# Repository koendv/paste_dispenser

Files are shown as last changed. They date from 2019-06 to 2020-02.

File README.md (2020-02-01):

# Solder Paste Dispenser

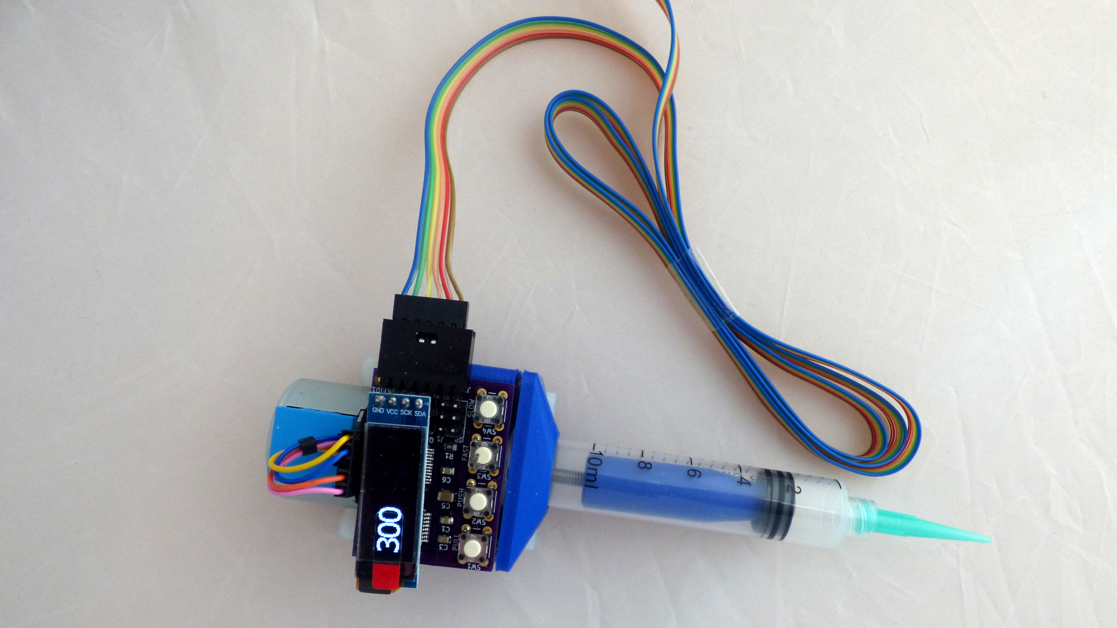
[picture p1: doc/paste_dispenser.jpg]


This is a solder paste dispenser. The controller supports unipolar and bipolar stepper motors, a foot pedal switch, an OLED display, a LED that blinks faster when the motor runs faster, and a menu system. The board has been designed with easy soldering in mind, using components size 0805 and up.

## Foot switch
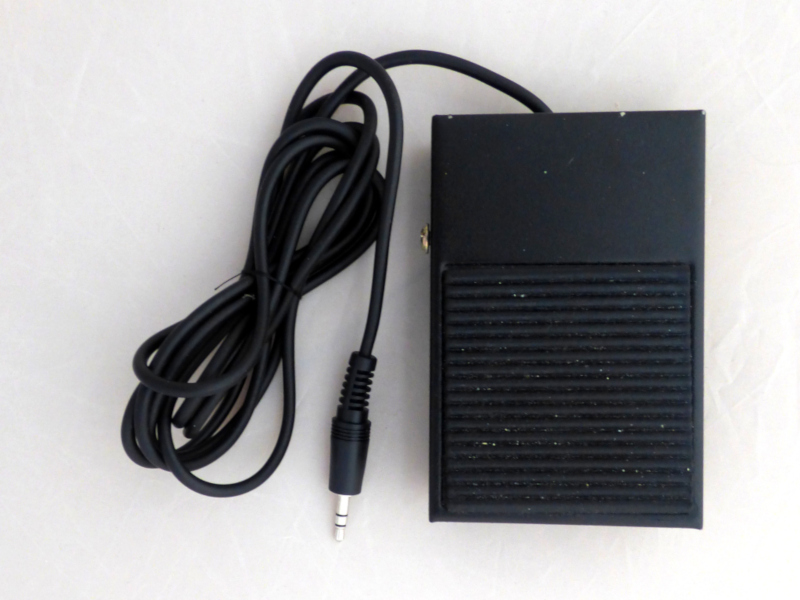
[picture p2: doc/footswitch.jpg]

Dispensing can be initiated either by pressing the *push* button on the dispenser, or by pushing down a foot pedal switch.

A foot pedal switch has the advantage that it frees up a hand. Using a foot switch is also more stable; pushing a button on the solder dispenser always moves the syringe tip a little bit.

Suitable foot pedals are [Adafruit product ID 423](https://www.adafruit.com/product/423) and [Sparkfun COM-11192](https://www.sparkfun.com/products/11192), and their equivalents at ebay and aliexpress.

These foot pedal switches are simple on/off switches, normally open. Speed controller foot pedals with a potentiometer will **not** work.

## Display

The display shows the motor speed.

The OLED display is a generic OLED module 0.91" diagonal, 128x32 pixel, I2C, SSD1306, as found on ebay, aliexpress and [others](https://www.google.com/search?q=OLED+module+0.91%22+128x32+I2C+SSD1306+price). Before buying, check the module has a 4-pin connection - GND, VCC, SDA, SCK - and uses a SSD1306 controller. The display *ought* not to touch any of the components below, but you can always put a bit of Kaptan tape on the back of the display, just to make sure.

The OLED display is optional. If you choose not to install the OLED display you can still check stepper speed on the serial console.

## Menu

There is a settings menu on the serial port. The serial port runs at 115200, 8N1, no flow control. Access the menu using a vt100 ansi terminal emulation, e.g. [PuTTY](https://putty.org/) on Windows, or *minicom* on Linux. On Android, use an USB OTG adapter and *Serial USB Terminal*. The settings menu allows you to configure forward speed, backward speed, pullback, and microstepping, and to store and recall these settings from non-volatile memory. The menu looks like this:

	[f] Forward speed 125 steps/sec
	[s] Forward steps 0 steps
	[b] Backward speed 500 steps/sec
	[d] Pullback delay 2000 millisec
	[p] Pullback steps 0 steps
	[m] Microstepping 2
	[n] Profile number 0
	[r] Restore profile
	[w] Save profile
	[h] Help

### Speed
Forward speed can be set using the *faster*/*slower* buttons on the dispenser itself or using the console menu.

If *forward steps* is zero, the syringe plunger is pushed down as long as you press the *push* button or the foot switch pedal. This is useful for making beads, and the normal setting when dispensing solder paste. If *forward steps* is non-zero, pushing the *forward* button or the foot switch moves the plunger down exactly the number of steps in the settings. This is useful for making precise, repeatable dots, e.g. as a glue or lubricating oil dispenser.

Backward speed can only be set using the console menu.

### Pullback
Sometimes liquid keeps oozing out after you stop dispensing. If *pullback steps* is non-zero, then after a *pullback delay* period of inactivity the plunger will move back *pullback steps*, to stop liquid oozing out. How successful this is and how many steps the plunger needs to pull back to stop the oozing depends upon the viscosity of the liquid. *Pullback* works better with low viscosity liquids than with high viscosity paste. Pullback is interesting if you use this as a dispenser for e.g. cyanoacrylate glue.

### Microstepping
The controller supports up to 1/64 microstepping. This is open loop voltage control microstepping.
Choose speed and microstepping that goes well with your stepper motor. This may take a bit of trial and error. Default is half-stepping, suitable for 28BYJ-48 steppers .

### Saved Profiles

Once you have found a setting that works, you can save it for later. Up to five profiles can be saved. These profiles are remembered even when the power is turned off. After power-up the last saved settings are used.

## Power supply

If you want to play it safe, use a 5.0V 1A phone charger as power supply. The TB6612 stepper motor driver IC supports 5V 1.2A continuous, but can be damaged by higher currents. Using a power supply with a maximum current less than 1.2A protects the driver IC in case of short circuit or stall.

The voltage range is 4.5V to 5.5V. More than 5.5V is too much for the atmega328p microcontroller; less than 4.5V and the TB6612 stepper driver stops working.

The board has a MOSFET for reverse polarity protection.

## Connecting everything

The controller board has four headers:

* J1 is the ISP connector for downloading the initial firmware to the atmega microcontroller.
* J2 connects to an USB to serial adapter (pins +5V, RX, TX, GND) and the footswitch (pins FTSW, GND). The footswitch is optional, but very handy.
* J3 is the connector for the stepper motor. Both unipolar and bipolar steppers can be connected. Connect one coil to pins A1 and A2, and one coil to pins B1 and B2. Connect the center tap of unipolar steppers to pin GND.
* J4 is the connector for the optional OLED display. Solder a 4-position female Dupont housing here.

## Bootstrapping

The first compile is the hardest.

Open the Arduino IDE. Compile the *paste dispenser* sketch, with these settings:

* Board: Arduino Pro or Pro Mini,
* Processor: Atmega328P (5V, 16MHz).

Generate an Intel Hex file with _Sketch -> Export Compiled Binary_. This creates two .hex files in the project directory, `arduino.ino.eightanaloginputs.hex` and `arduino.ino.with_bootloader.eightanaloginputs.hex`. The hex file we need is the one with the bootloader.
The ISP programmer is an arduino with the same logic levels as the target system. As the solder paste dispenser uses 5V logic, we need an Arduino with 5V logic levels as ISP programmer. Connect a 5V Arduino, e.g. an Arduino Uno, to your system. Compile and upload the _File -> Examples -> ArduinoISP_ sketch to the Uno. Connect the Arduino Uno to the solder paste dispenser board as follows:

Signal|Uno    |ISP pin
------|-------|--------
RST	|Uno pin 10|5
MOSI|Uno pin 11|4
MISO|Uno pin 12|1
SCK|Uno pin 13|3
VCC|Uno 5V|2
GND|Uno GND|6

Find `avrdude` in your Arduino IDE directories, change to the appropriate directory and do the following incantation:

	koen@raspberrypi:/opt/arduino-1.8.9/hardware/tools/avr $ ./bin/avrdude -C ./etc/avrdude.conf -p m328p -P /dev/ttyACM0 -c avrisp -b 19200 -U flash:w:/home/koen/src/paste_injector/arduino/arduino.ino.with_bootloader.eightanaloginputs.hex

where `/dev/ttyACM0` is the usb port of your Arduino Uno. Flashing should take about 20 seconds, and ends with "`xxx bytes of flash verified`" and "`Fuses OK`".

Set the fuses of the atmega328p for an external resonator at 16MHz:

	koen@raspberrypi:/opt/arduino-1.8.9/hardware/tools/avr $ ./bin/avrdude -C ./etc/avrdude.conf -c avrisp -p m328p -P /dev/ttyACM0 -b 19200  -U lfuse:w:0xff:m -U hfuse:w:0xda:m -U efuse:w:0xfd:m

The avrdude output ought to say: ```avrdude: safemode: Fuses OK (E:FD, H:DA, L:FF)```

If you just want to read the fuses:

	koen@raspberrypi:/opt/arduino-1.8.9/hardware/tools/avr $  ./bin/avrdude -C ./etc/avrdude.conf -c avrisp -p m328p -P /dev/ttyACM0 -b 19200 -U lfuse:r:-:i -v

This finishes writing bootloader and sketch to the solder paste dispenser. Disconnect the Arduino Uno. The atmega328p now contains a bootloader. Sketches can now be uploaded using the solder paste dispenser serial port.

## Firmware

The solder paste dispenser is an arduino system. Once the bootstrap loader has been installed the solder paste dispenser can be programmed using the arduino IDE.

To avoids spurious resets when connecting to the serial port, there is no capacitor between DTR and reset. But this also means that if you want to develop firmware for this board there is no automatic reset before uploading. Three options:

* Upload firmware using the ISP connector. This has to be done at least once, to upload the bootloader.
* Use the serial port to upload. This is what I usually do. Before uploading connect RST and ground with a Dupont jumper wire. RST and ground are next to each other on the ISP connector. In the Arduino IDE, click Sketch -> Upload, count to three and remove the jumper wire.
* When developing connect a 100n capacitor between serial adapter DTR and ISP connector RST pin. This allows the IDE to reset the microcontroller automatically just before uploading using the serial port.

## Soldering your own
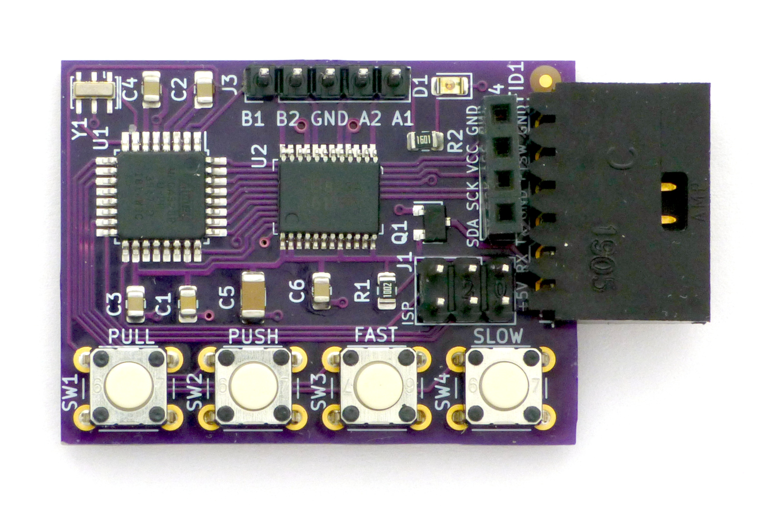
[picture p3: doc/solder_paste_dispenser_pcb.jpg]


The github contains arduino source and kicad pcb design files. You'll find the [schematic](https://github.com/koendv/paste_dispenser/raw/master/kicad/paste_dispenser/paste_dispenser_schematic.pdf), the [board layout](https://github.com/koendv/paste_dispenser/raw/master/kicad/paste_dispenser/paste_dispenser_board.pdf), and the [bill of materials](https://github.com/koendv/paste_dispenser/blob/master/kicad/paste_dispenser/paste_dispenser.csv). This is a link to the pcb as an orderable [shared project at oshpark](http://www.oshpark.com/shared_projects/V5txbi41), and these are the components as a [shared project at Mouser](https://www.mouser.com/ProjectManager/ProjectDetail.aspx?AccessID=61ff8d7d43). Here are [zipped gerbers](https://github.com/koendv/paste_dispenser/raw/master/kicad/paste_dispenser/gerbers.zip) for pcb manufacturing at [jlcpcb](https://jlcpcb.com/).

If you prefer not to solder SMD's you can also build the controller on a breadboard or as a through-hole pcb, as in this [fritzing sketch](https://github.com/koendv/paste_dispenser/raw/master/fritzing/paste_dispenser_fritzing_breadboard.pdf) of a 5V 16MHz Arduino Pro Mini and a TB6612 breakout module.

## Printing your own
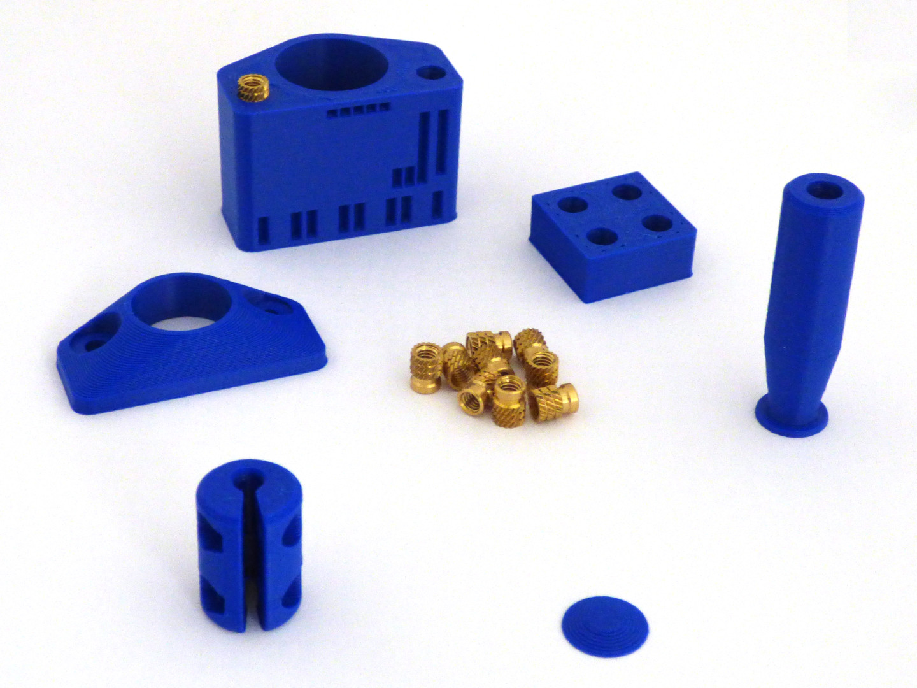
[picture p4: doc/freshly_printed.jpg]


Leave part orientation as is when imported into PrusaSlicer. Designed to print without support.

The [openscad/](https://github.com/koendv/paste_dispenser/tree/master/openscad) directory contains the .stl files for [3d-printing](https://www.treatstock.com/c/seaside-3d) the mechanical part of the solder paste dispenser in ABS using FDM. These parts need finishing as follows:

* Take the workpiece [insert_practice](https://github.com/koendv/paste_dispenser/blob/master/openscad/aerzetix-C19143/insert_practice.stl) and place 4 heat-set inserts, as a test. Set your soldering iron to the filament extrusion temperature used during 3D printing, about 255&deg;C.
* Take the workpiece [motor_mount](https://github.com/koendv/paste_dispenser/blob/master/openscad/aerzetix-C19143/motor_mount.stl) and place 4 heat-set inserts.
* Take the workpiece [plunger](https://github.com/koendv/paste_dispenser/blob/master/openscad/aerzetix-C19143/plunger.stl) and place 1 heat-set insert.
* Using **a drop** of acetone, glue the small conical [plunger tip](https://github.com/koendv/paste_dispenser/blob/master/openscad/aerzetix-C19143/plunger_tip.stl) to the plunger. Acetone is a solvent for ABS.

Mechanical assembly is next.
## Assembly
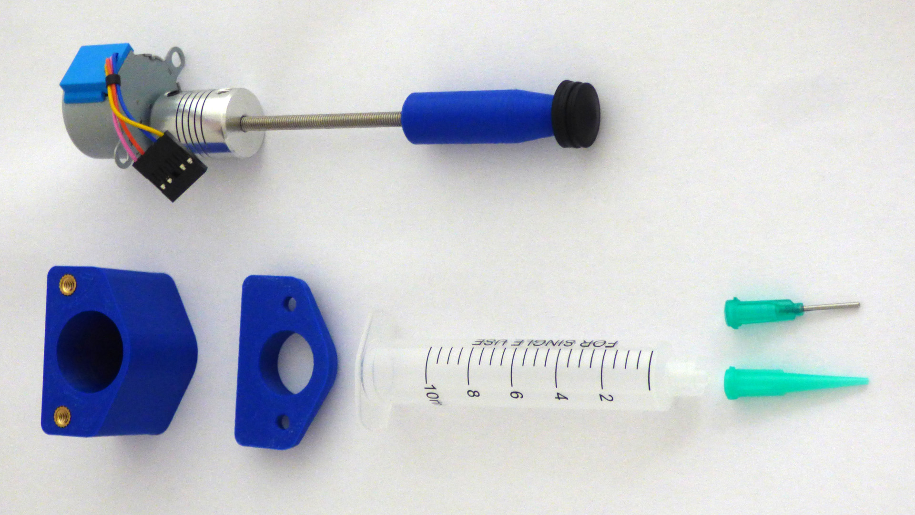
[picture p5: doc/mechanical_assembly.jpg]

The mechanical part consists of stepper motor, coupler and leadscrew. 

The stepper motor is a [28BYJ-48](https://www.adafruit.com/product/858). The motor can be used "as is", or [modified to bipolar](https://coeleveld.com/wp-content/uploads/2016/10/Modifying-a-28BYJ-48-step-motor-from-unipolar-to-bipolar.pdf) for additional torque.

The leadscrew is 64mm of M4 threaded rod, 0.7mm pitch. The leadscrew mates with the M4 threaded insert in the plunger.

The coupler between motor and leadscrew is an [Aluminum 4mm to 5mm shaft couplers](https://www.google.com/search?&q=%2B%22D19*L25%22+Shaft+Coupling+Aluminium+flexible+%2B%224x5%22+aliexpress), readily available from ebay or aliexpress. The all-metal construction easily handles the torque.

Attach the stepper motor to the motor mount using two nylon or stainless steel M4x10 hex socket screws. Nylon screws keep the weight down. Attach the [syringe holder](https://github.com/koendv/paste_dispenser/blob/master/openscad/aerzetix-C19143/syringe_holder.stl) to the motor block with two M4x10 hex socket screws.

The syringe used is a BD 10cc "Luer-Lok", or one of its many [oriental clones](https://www.google.com/search?q=10cc+syringe+smt+smd+site%3A.aliexpress.com). Remove the black rubber piston head from the syringe and put it on the solder paste dispenser plunger.

Friction between rubber piston and syringe is what keeps the plunger from spinning. If during operation the plunger rotates instead of moving forward, clean the sides of the black rubber piston head with (isopropyl) alcohol to remove any grease. 

## Adding the Electronics
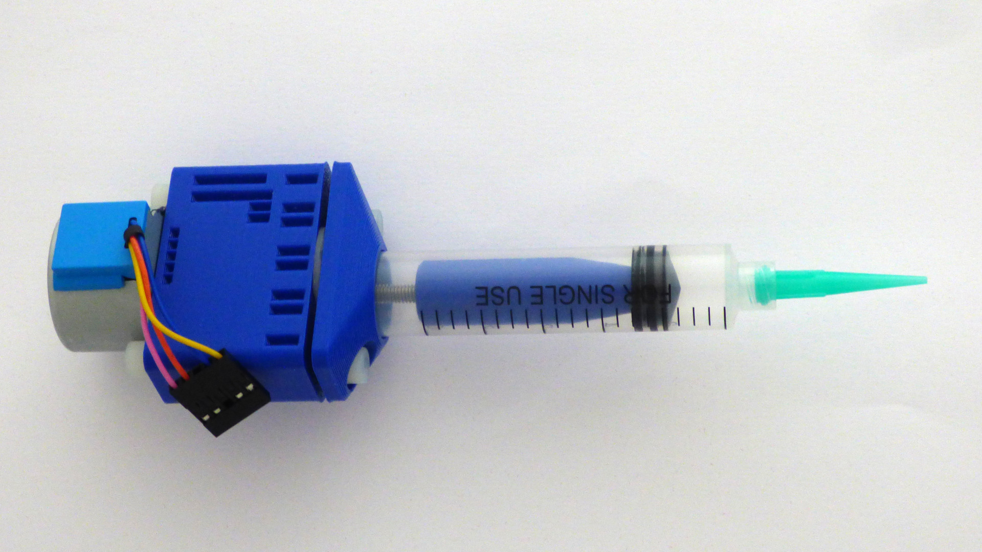
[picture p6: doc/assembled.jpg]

Align the pins of the PCB with the holes in the front of the motor mount. Fix the PCB in place with adhesive Velcro tape. Plug the OLED display in the connector marked "SDA SCK VCC GND". Connect the stepper motor to header J3.

Run 1-2m of cable from the 6-pin Dupont connector on the right of the PCB. The cable connects solder paste dispenser to a [5V TTL serial to USB converter](https://www.google.com/search?q=CH340C+site%3A.aliexpress.com) (pins +5V,RX,TX,GND) and the foot switch (pins FTSW, GND). 

If the motor turns the wrong way, swap pins A1 and A2, or pins B1 and B2.

At this point you have a working solder paste dispenser, ready for use.

## Practice makes perfect

For practice fill a syringe with a small amount (approx. 1 ml) of toothpaste. Print a pcb at scale 1:1 in black and white on paper and practice depositing toothpaste until you are comfortable with the solder paste dispenser.

Before filling the syringe, run a nylon wire inside the syringe body. A small piece of fishing line is suitable. This nylon wire creates a small leak in the seal between plunger and syringe body, allowing the air to escape while you push the plunger down. Once the plunger is down, simply pull the nylon wire out and you can begin dispensing.

## Notes

* There are a few situations which may result in breakage.
If the piston pushes against the bottom of an empty syringe, something has to give.
Likewise, if you try to squeeze paste out of a stoppered syringe.
In general, avoid "unstoppable force meets inmovable object" situations. Something will break - the motor may tear itself off its mounts, for instance.

* When not in use, loosen the syringe holder screws so the syringe isn't under constant pressure.

* A solder paste dispenser is a small motor which pushes the plunger of a syringe. You can use it for solder paste or solder flux, but the dispenser can also be used as a syringe pump, to create small dots of glue in a precise and repeatable way, or to put small drops of lubricating oil on a mechanism.

* The controller is not restricted to any specific model of solder paste dispenser; if a syringe pump uses a 5- or 6-wire unipolar or a 4-wire bipolar stepper motor, there's a reasonable chance this will work. Just check the stepper works at 5V and current stays below 1.2 amps.

* FDM print settings: Increase perimeters on the pieces with heat-set inserts ([motor_mount](https://github.com/koendv/paste_dispenser/blob/master/openscad/aerzetix-C19143/motor_mount.stl) and [plunger](https://github.com/koendv/paste_dispenser/blob/master/openscad/aerzetix-C19143/plunger.stl)); this gives the heat-set inserts more material to grip onto. 

* Exactly how hard do we need to push? Take a syringe and (kitchen) scales. Grab the syringe by the syringe body, and push the syringe piston against the scales until the syringe releases solder paste. Take note of the weight the scales indicate. If the scales indicates pounds, multiply by 5 to get Newtons. If the scales indicate kilogrammes, multiply by 10 to get Newtons.
Measured this way, pushing the plunger of 5cc and 10cc syringes of solder flux and solder paste needs a force between 20N and 30N.

* The kicad pcb hardware design is under Creative Commons - Attribution Share Alike license.

* This design was inspired by solder paste dispensers by [zapta](https://www.thingiverse.com/thing:1119914) and [geir](https://www.thingiverse.com/thing:384680). The mechanical part is a remix of zapta's, with only minor changes.

* This design was built around a Atmega328p "Pro Mini" and a TB6612 stepper driver. An alternative design would be a STM32F103 "Black Pill" and a TMC2130 SilentStepStick stepper driver. The STM32F103 has enough cpu to run a comprehensive menu system and built-in usb. The TMC2130 stall detection allows detecting when the plunger has reached the bottom of the syringe, so software can move the plunger back a few steps before any mechanical damage occurs. But such a design would hit a different price point.

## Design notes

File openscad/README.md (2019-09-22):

The is a remix of the ["zapta" Arduino Motorized SMT Solder Paste Dispenser](https://www.thingiverse.com/thing:1119914) , with the following mods:

- stepper controller board with support for footswitch
- motor mount with holes for solder-side pins of the stepper controller board.
- 28BYJ-48 stepper motor converted from [unipolar to bipolar](http://www.jangeox.be/2013/10/change-unipolar-28byj-48-to-bipolar.html) for more torque
- [aluminum 4mm to 5mm shaft coupler](https://www.google.com/search?&q=%2B%22D19*L25%22+Shaft+Coupling+Aluminium+flexible+%2B%224x5%22+aliexpress) instead of a 3D-printed ABS shaft coupler

These parts have been designed with [openscad](http://www.openscad.org), a programming language for creating 3D-printable objects.

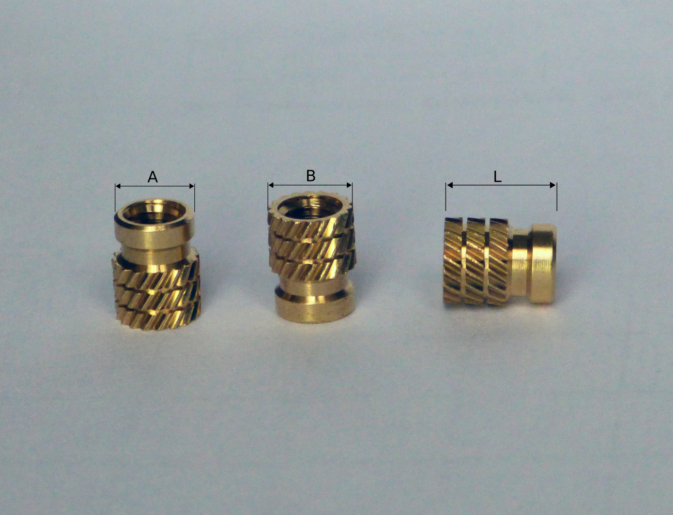
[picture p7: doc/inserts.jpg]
knurled threaded tapered brass insert


This build requires 5 M4 threaded inserts, type *IUB-M4-2*. You push these [heat-set inserts](https://www.lulzbot.com/learn/tutorials/heat-set-inserts-tips-and-tricks) in with a hot soldering iron (approx. 255 &deg;C). You may want to practice on [insert_practice.stl](https://github.com/koendv/paste_dispenser/blob/master/openscad/mcmaster-94180A353/insert_practice.stl) first.

The file m4_threaded_insert.scad allows you to choose between [McMaster-Carr 94180a353](https://www.mcmaster.com/94180a353) (McMaster, US) and [Aerzetix C19143](https://www.amazon.co.uk/dp/B075XHV3GH/) (Amazon, Europe) inserts. Before generating .stl files in [openscad](http://www.openscad.org), edit m4_threaded_insert.scad and uncomment the threaded insert used. 

If the heat-set inserts you wish to use are not defined in m4_threaded_insert.scad, you can easily add your own. With a caliper measure the dimensions of the heat-set insert, as in the picture above. Add slack for the printing process, and add the dimensions of the heat-set insert to m4_threaded_insert.scad.

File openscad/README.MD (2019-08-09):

The is a remix of the ["zapta" Arduino Motorized SMT Solder Paste Dispenser](https://www.thingiverse.com/thing:1119914) , with the following mods:

- add holes for solder-side pins of the stepper controller board.
- convert 28BYJ-48 stepper motor from [unipolar to bipolar](http://www.jangeox.be/2013/10/change-unipolar-28byj-48-to-bipolar.html) for more torque
- use an [aluminum 4mm to 5mm shaft coupler](https://www.google.com/search?&q=%2B%22D19*L25%22+Shaft+Coupling+Aluminium+flexible+%2B%224x5%22+aliexpress) instead of a 3D-printed shaft coupler

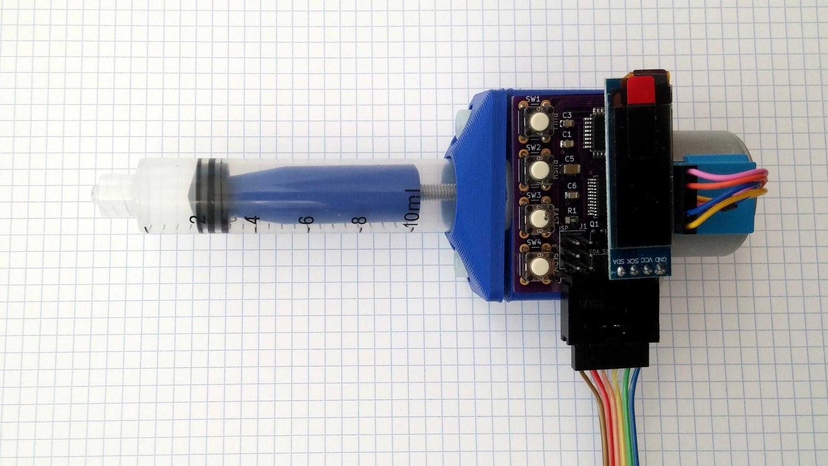
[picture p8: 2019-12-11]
doc/ready.jpg

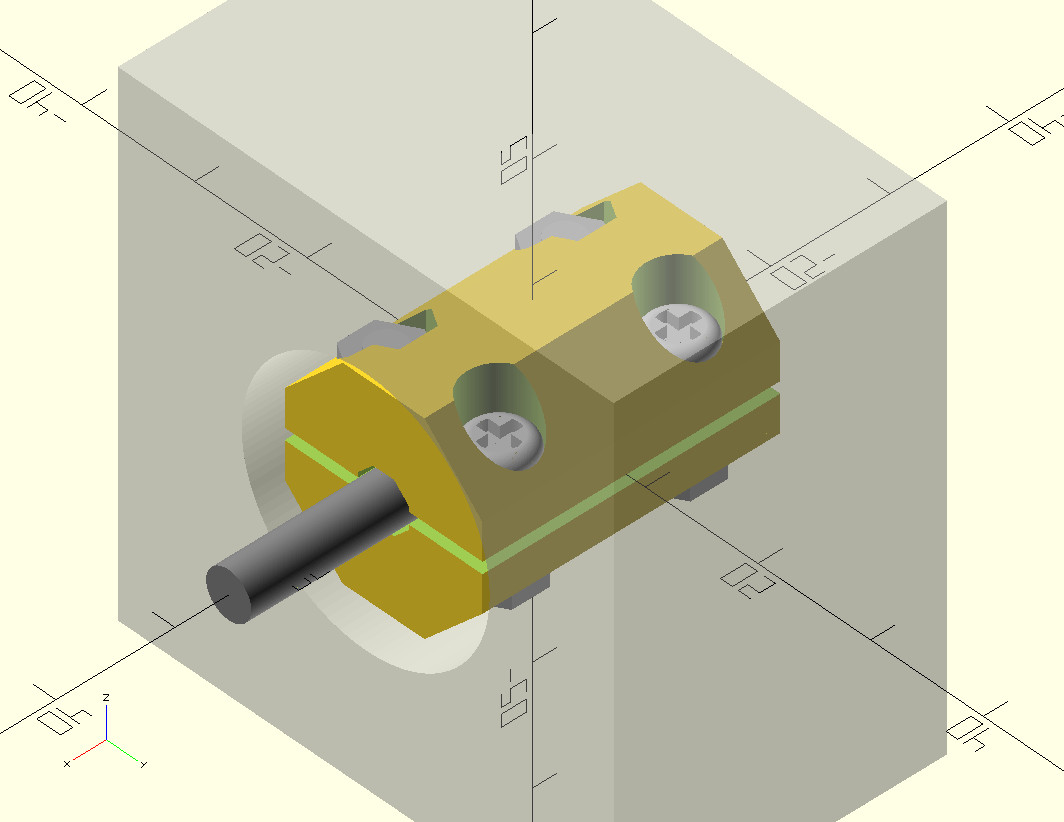
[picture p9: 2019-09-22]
doc/coupler.jpg

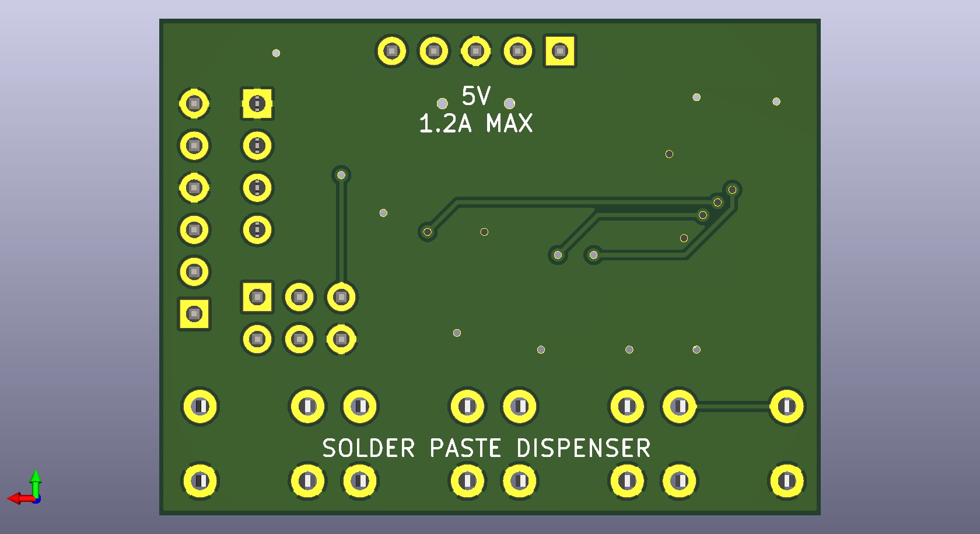
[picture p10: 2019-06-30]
kicad/paste_dispenser/paste_dispenser_back.png

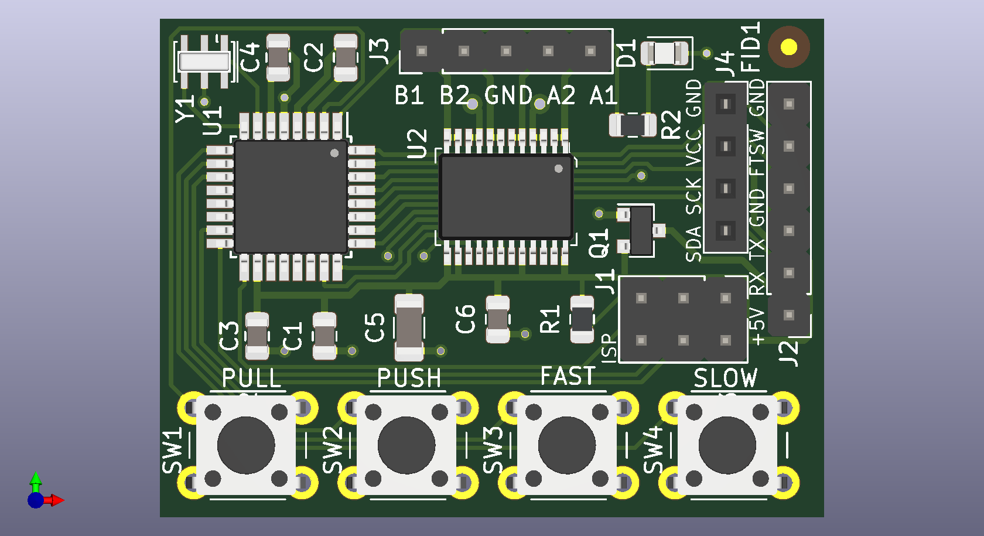
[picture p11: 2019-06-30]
kicad/paste_dispenser/paste_dispenser_front.png

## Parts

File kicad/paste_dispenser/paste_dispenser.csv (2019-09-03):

Title | Solder Paste Dispenser
Revision | 1
Date | 5/26/19
Generated | Sun 30 Jun 2019 08:40:43 AM CEST
Company
Comment 1 | Koen De Vleeschauwer
Comment 2 | Released under the Creative Commons Attribution-ShareAlike 4.0 license.
Comment 3
Comment 4
Total Parts | 24
Total Unique Parts | 16
Ref | Qty | Value | Footprint | Manufacturer | Manufacturer Part No | Source 1 | Source 1 Part No | Source 2 | Source 2 Part No | Note
C2 C3 C6 C4 | 4 | 100n | Capacitor_SMD:C_0805_2012Metric | Yageo | CC805KRX7R7BB104 | mouser.com | 603-CC805KRX7R7BB104
C1 | 1 | 10u | Capacitor_SMD:C_0805_2012Metric | Yageo | CC805KKX5R7BB106 | mouser.com | 603-CC805KKX5R7BB106
C5 | 1 | 22u | Capacitor_SMD:C_1206_3216Metric | Taiyo Yuden | EMK316BB7226ML-T | mouser.com | 963-EMK316BB7226ML-T
D1 | 1 | LED Yellow 2mA | LED_SMD:LED_0805_2012Metric | Kingbright | APTD2012LSYCK | mouser.com | 604-APTD2012LSYCK
FID1 FID2 FID3 | 3 | Fiducial | Fiducial:Fiducial_1mm_Dia_2.54mm_Outer_CopperTop
J1 | 1 | ISP | Connector_PinHeader_2.54mm:PinHeader_2x03_P2.54mm_Vertical | Adafruit | 2822 | mouser.com | 485-2822 |  |  | 2x20 breakaway header break off 2x03 strip
J4 | 1 | OLED | Connector_PinSocket_2.54mm:PinSocket_1x04_P2.54mm_Vertical | Harwin | M20-7820442 | mouser.com | 855-M20-7820442
J3 | 1 | STEPPER | Connector_PinHeader_2.54mm:PinHeader_1x05_P2.54mm_Vertical | - | DNP
J2 | 1 | EXT | Connector_PinHeader_2.54mm:PinHeader_1x06_P2.54mm_Vertical | Harwin | M20-9750642 | mouser.com | 855-M20-9750642 |  |  | Mates with Dupont connectors
Q1 | 1 | SSM3J328R_LF | Package_TO_SOT_SMD:SOT-23 | Toshiba | SSM3J328R LF | mouser.com | 757-SSM3J328RLF
R1 | 1 | 10k | Resistor_SMD:R_0805_2012Metric | Yageo | AC0805FR-0710KL | mouser.com | 603-AC0805FR-0710KL
R2 | 1 | 1k6 | Resistor_SMD:R_0805_2012Metric | Yageo | AC0805FR-071K6L | mouser.com | 603-AC0805FR-071K6L
SW2 SW1 SW3 SW4 | 4 | SW_PB | Button_Switch_THT:SW_PUSH_6mm | Omron | B3F-1000 | mouser.com | 653-B3F-1000
U1 | 1 | ATmega328P-AU | Package_QFP:TQFP-32_7x7mm_P0.8mm | Microchip | ATMEGA328P-AU | mouser.com | 556-ATMEGA328P-AU
U2 | 1 | TB6612FNG_C_8_EL | digikey-footprints:LSSOP-24_W5.6mm | Toshiba Semiconductor and Storage | TB6612FNG C 8 EL | mouser.com | 757-TB6612FNGC8EL | digikey.com | TB6612FNGC8ELCT-ND
Y1 | 1 | 16MHz | Crystal:Resonator_SMD_muRata_CSTxExxV-3Pin_3.0x1.1mm_HandSoldering | Murata | CSTNE16M0V530000R | mouser.com | 81-CSTNE16M0V530000R
BOM made with KICAD_BOM_WIZARD (https://github.com/HashDefineElectronics/KiCad_BOM_Wizard.git)
Generated Sun 30 Jun 2019 08:40:43 AM CEST
Additionally the following items:
 | 1 |  | OLED module, 0.91", 128x32, I2C, SSD1306 |  |  | ebay.com |  | aliexpress.com |  | Check module has a 4-pin connection: GND, VCC, SDA, SCK and uses SSD1306 controller.
 | 1 |  | Footswitch, normally open, dry contact | Adafruit | 423 | mouser.com | 485-423 | aliexpress.com |  | These foot pedals are simple on/off switches. Speed controller foot pedals with a potentiometer will not work.
 |  |  | _OR_
 | 1 |  | Footswitch, normally open, dry contact | Sparkfun | COM-11192 | mouser.com | 474-COM-11192 | aliexpress.com |  | Footswitches: choose one.
 | 1 |  | usb to 5V TTL serial converter |  |  | ebay.com | FTDI FT232RL USB to 5V TTL Serial | aliexpress.com |  | For the serial console.
not truncated

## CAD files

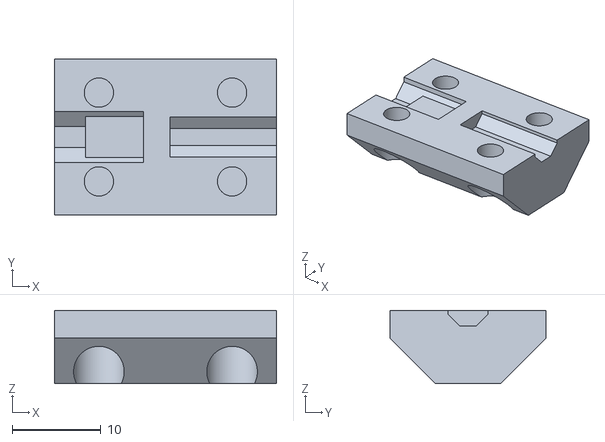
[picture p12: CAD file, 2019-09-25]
openscad/aerzetix-C19143/coupler.stl
25.0 x 17.6 x 8.28

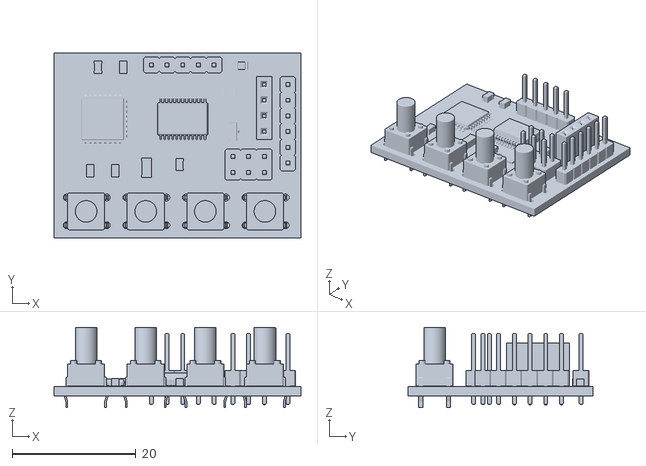
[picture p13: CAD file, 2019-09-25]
openscad/paste_dispenser.stl
40.0 x 30.0 x 13.0

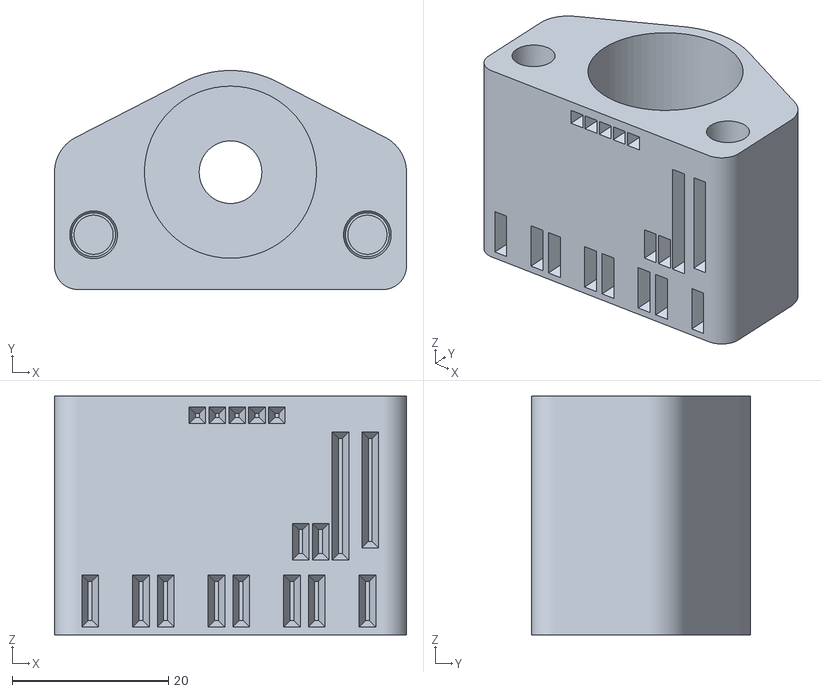
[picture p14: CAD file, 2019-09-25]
openscad/aerzetix-C19143/motor_mount.stl
45.0 x 28.0 x 30.5

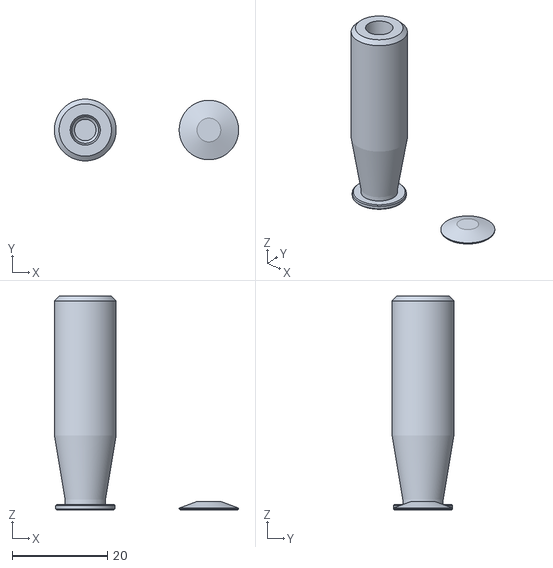
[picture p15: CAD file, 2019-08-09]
openscad/plunger.stl
38.8 x 13.0 x 45.0

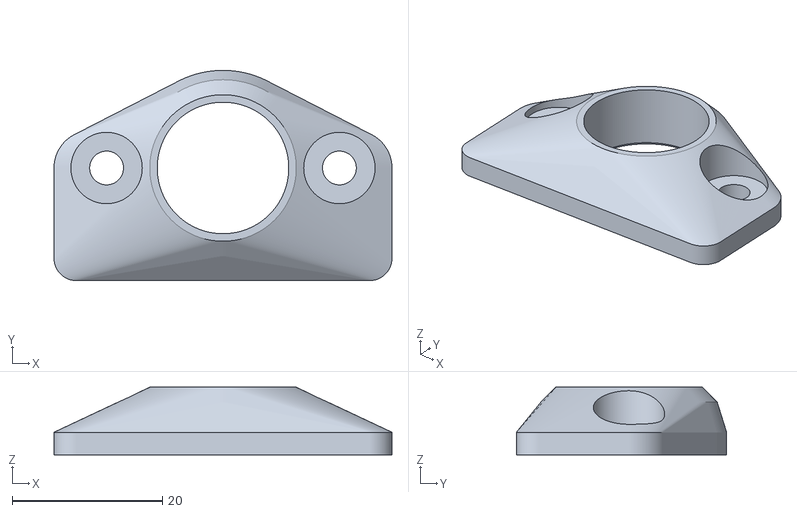
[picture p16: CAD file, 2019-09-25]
openscad/aerzetix-C19143/syringe_holder.stl
45.0 x 28.0 x 9.00

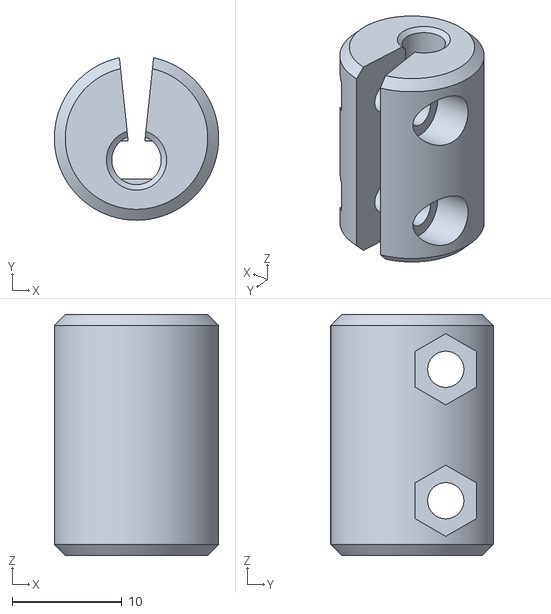
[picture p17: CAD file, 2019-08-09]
openscad/coupler.stl
15.0 x 14.8 x 22.0

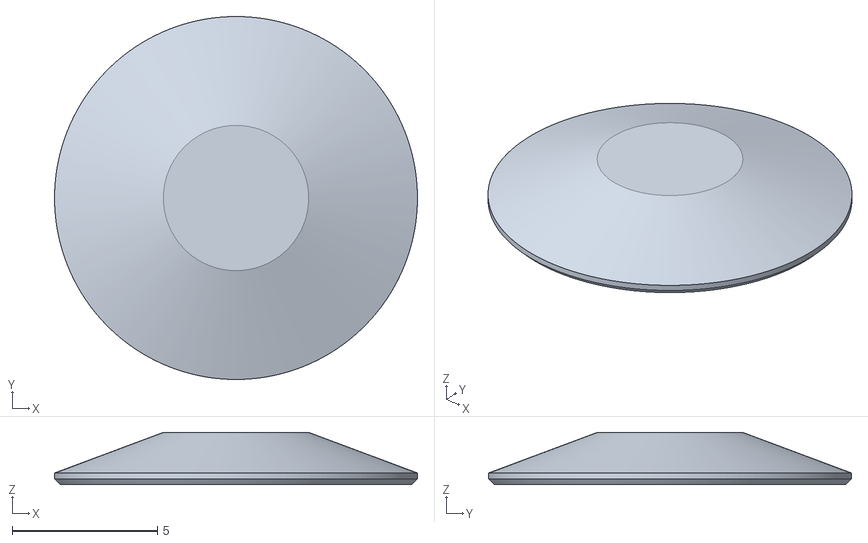
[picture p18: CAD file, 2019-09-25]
openscad/aerzetix-C19143/plunger_tip.stl
12.5 x 12.5 x 1.80

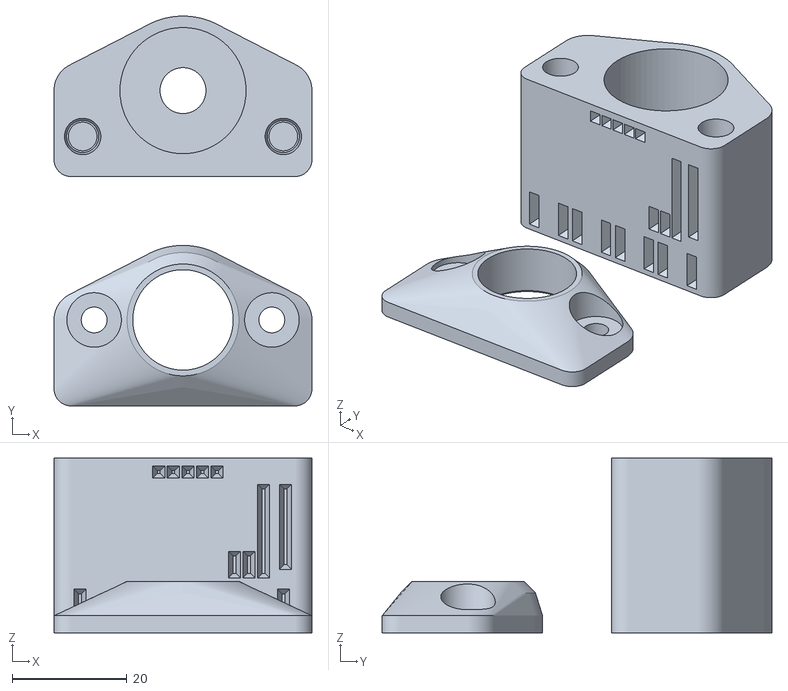
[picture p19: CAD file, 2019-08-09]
openscad/motor_mount.stl
45.0 x 68.0 x 30.5

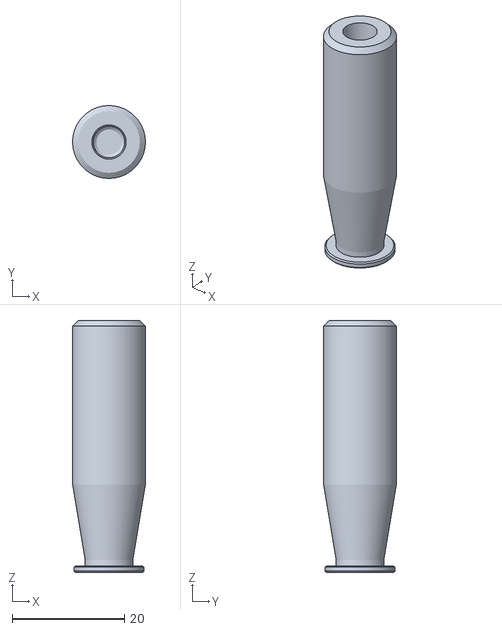
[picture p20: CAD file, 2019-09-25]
openscad/aerzetix-C19143/plunger.stl
13.0 x 13.0 x 45.0

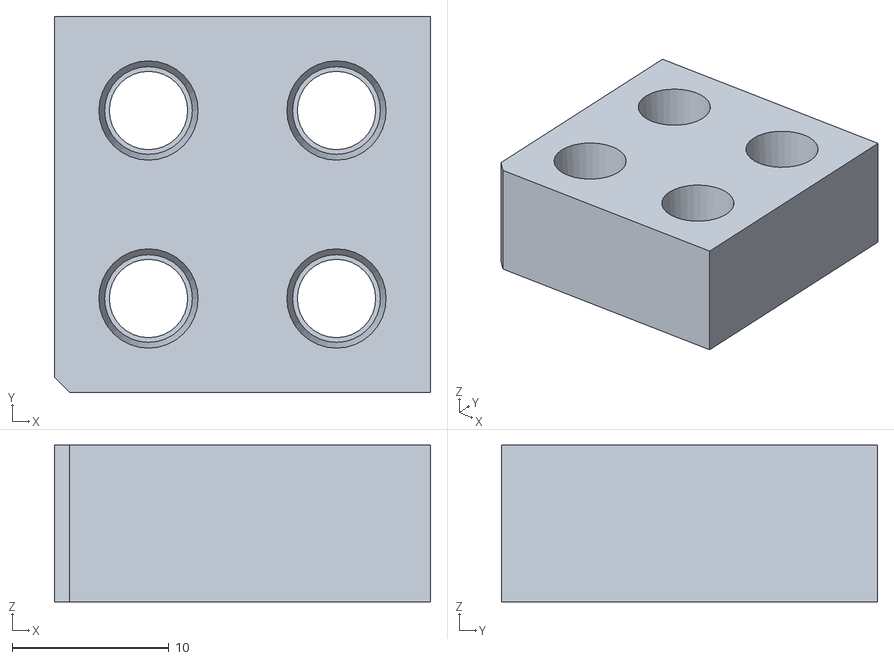
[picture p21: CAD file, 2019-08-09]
openscad/insert_practice.stl
24.0 x 24.0 x 10.0

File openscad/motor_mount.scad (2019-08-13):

// This file generates two parts, the motor mount and a matching syringe holder plate.
// The motor mount has holes for 4 M4 threaded inserts, McMaster 94180A353. Push them
// in with a standard solder iron. Make sure to push 1-2 mm at a time, letting the 
// plastic part to cool down.

$fn=180;

shaft_hole_diameter = 8;

bottom_height = 2.5;
motor_mount_width = 45;

cavity_wall = 2;
cavity_height = 28;
cavity_diameter = 22;

motor_screws_space = 35;
motor_screws_holes_offset = 8;
motor_screws_holes_depth = 20;

syringe_screws_space = 31;
syringe_screws_holes_depth = 20;

total_height = bottom_height + cavity_height;

base_corner_radius1 = 5;  // convex side
base_corner_radius2 = 3;  // flat side
base_corner_offset  = 0;

syringe_holder_height1 = 3;
syringe_holder_height2 = 6;
syringe_hole_diameter = 16.5+1.0;
syringe_hole_wall = 3;

syringe_holder_screw_diameter = 4.0+0.5;
syringe_holder_screw_head_diameter = 9.0+0.5;

chamfer = 0.5;

eps1 = 0.001;
eps2 = 2*eps1;

pcb_solder_side_components = 2.0;

include <pcb.scad>

// Hole for a M4 metal insert, mcmaster part number 94180A353.
// h is the total depth for the screw hole. Already includes an 
// extra eps1 at the opening side.
module m4_threaded_insert(h) {
  include <m4_threaded_insert.scad>
  translate([0, 0, -eps1]) {
    // NOTE: diameter are compensated to actual print results.
    // May vary among printers.
    cylinder(d1=B, d2=A, h=eps1+L*2/3, $f2=32);
    cylinder(d=A, h=eps1+L, $f2=32);
    translate([0, 0, L-eps1]) cylinder(d=D, h=h+eps1-L, $f2=32);
  }
}

// c1, c2 are chamfers at bottom and top respectivly. s1, s2 are chamfers's slopes.
module chamfered_cylinder(d, h, c1, s1, c2, s2) {
    cylinder(d1=d-2*c1, d2=d, h=s1*c1);
    translate([0, 0, s1*c1-eps1]) cylinder(d=d, h=h-s1*c1-s2*c2+eps2);
    translate([0, 0, h-s2*c2]) cylinder(d1=d, d2=d-2*c2, h=s2*c2);
}

module motor_holes() {
  translate([motor_screws_space/2, -motor_screws_holes_offset, total_height]) 
      rotate([180, 0, 0]) 
      m4_threaded_insert(motor_screws_holes_depth);

 translate([-motor_screws_space/2, -motor_screws_holes_offset, total_height]) 
      rotate([180, 0, 0]) 
      m4_threaded_insert(motor_screws_holes_depth);
}

module syringe_screws() {
  translate([syringe_screws_space/2, 0, -eps1]) 
      m4_threaded_insert(syringe_screws_holes_depth);
  
  translate([-syringe_screws_space/2, 0, -eps1]) 
       m4_threaded_insert(syringe_screws_holes_depth);
}

// Hole at the bottom of the base for the shreded shaft.
module shaft_hole() {
 translate([0, 0, -eps1]) cylinder(d=shaft_hole_diameter, h=bottom_height+eps2, $f2=32);
}

// The motor mount before any substraction. It accepts a height parameter so 
// we can use this pattern also for the syringe holder.
module base_pattern(h) {
  hull() {
    cylinder(d=cavity_diameter+2*cavity_wall, h=h);
    
    // Flat side
    translate([motor_mount_width/2-base_corner_radius2, -(cavity_diameter+2*cavity_wall)/2+base_corner_radius2-pcb_solder_side_components, 0]) cylinder(r=base_corner_radius2, h=h);
    
    translate([-(motor_mount_width/2-base_corner_radius2), -(cavity_diameter+2*cavity_wall)/2+base_corner_radius2-pcb_solder_side_components, 0]) cylinder(r=base_corner_radius2, h=h);
    
    // Concave side
    translate([motor_mount_width/2-base_corner_radius1, base_corner_offset, 0]) 
        cylinder(r=base_corner_radius1, h=h);
    
    translate([-(motor_mount_width/2-base_corner_radius1), base_corner_offset, 0]) 
        cylinder(r=base_corner_radius1, h=h);
  }
}

// The coupler cavity cut.
module cavity() {
  translate([0, 0, bottom_height]) cylinder(d=cavity_diameter, h=total_height, $fn=64);  
}

module motor_mount() {
  difference() {
    base_pattern(total_height);
    cavity();
    shaft_hole();
    motor_holes();
    syringe_screws();
    translate([0, -(cavity_diameter+2*cavity_wall)/2-pcb_solder_side_components-pcb_thickness+eps1, pcb_width/2])
    rotate([-90, 0, 0])
    pcb();  
  }
}

module syringe_holder_blank() {
  hull() {
    translate([0, 0, syringe_holder_height1]) rotate([0, 180, 0]) 
        base_pattern(syringe_holder_height1);
  
    chamfered_cylinder(syringe_hole_diameter+2*syringe_hole_wall, syringe_holder_height1+syringe_holder_height2, eps1, 1.0, 2.0, 1.0);
  } 
}

module syringe_holder() {
  total_h=syringe_holder_height1+syringe_holder_height2+eps2;
  difference() {
    syringe_holder_blank();
    
    // Syringe hole + chamfer;
    translate([0, 0, -eps1]) {
      cylinder(d=syringe_hole_diameter, h=total_h+eps2);
      cylinder(d1=syringe_hole_diameter + 2*chamfer, d2=eps1, 
          h=(syringe_hole_diameter + 2*chamfer)/2);
    }
    
    
    
    // Screw holes + chamfers.
    translate([-syringe_screws_space/2, 0, -eps1]) {
      cylinder(d=syringe_holder_screw_diameter, h=total_h+eps2);
      cylinder(d1=syringe_holder_screw_diameter + 2*chamfer, d2=eps1, 
          h=(syringe_holder_screw_diameter + 2*chamfer)/2);
    }
    
    translate([syringe_screws_space/2, 0, -eps1]) {
      cylinder(d=syringe_holder_screw_diameter, h=total_h+eps2);
      cylinder(d1=syringe_holder_screw_diameter + 2*chamfer, d2=eps1, 
          h=(syringe_holder_screw_diameter + 2*chamfer)/2);
    }
    
    // Screw heads insets.
    translate([-syringe_screws_space/2, 0, syringe_holder_height1]) 
        cylinder(d=syringe_holder_screw_head_diameter, h=syringe_holder_height2+eps2);
    
    translate([syringe_screws_space/2, 0, syringe_holder_height1]) 
        cylinder(d=syringe_holder_screw_head_diameter, h=syringe_holder_height2+eps2);
  }  
}

module main() {
  motor_mount();
  translate([0, -40, 0]) syringe_holder();
}

main();

 

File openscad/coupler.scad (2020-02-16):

// 28BYJ-48 stepper motor to M4 threaded shaft coupler.

// This prints half a coupler. To get a shaft coupler you need to print two of these.
// After printing remove the support from the screw holes by hand, with a 3mm drill.
// Clamp stepper shaft and leadscrew using four M3 x 10mm screws

// This file also contains an assembled model of the shaft coupler, stepper shaft and lead screw.

include <NopSCADlib/lib.scad>;
include  <util.scad>

coupler_height = 25.0;
coupler_width = 19.0;
coupler_slot_width = 1.0;
coupler_inradius = coupler_width/2 * cos(180/8);

eps1 = 0.001;
eps2 = 2 * eps1;
$fn = 120;
layer_thickness = 0.5;

// --- 28BYJ-48 stepper
// shaft diameter
stepper_shaft_dia = 5.0 + 0.7;
// Length of hole for shaft 1.
stepper_shaft_height = 10;
// Width between the flat sides of the motor shaft hole.
stepper_shaft_width = 3.0 + 0.5;
// Height of full round hole at the motor end.
stepper_shaft_base_height = 3.5;

// --- M4 threaded shaft end
// Inner diameter of hole for shaft 2. This one fits the M4 threaded shaft.
leadscrew_dia = 4.0 + 0.5;
// Length of hole for shaft 2.
leadscrew_height = 12;

// --- M3 Clamping screws
// Diameter of the screw holes.
screw_hole_diameter = 3.3;
// Diameter of the inset for the screws head.
screw_head_diameter = 5.7;
// Diameter of the inset for the screws nuts.
screw_nut_diameter = 6.5;
// Distance between screw head and nut.
screw_head_to_nut = 7.0;
// Offset of the screws' centers from the coupler's center.
hole_offset_from_center = 5.0;
// Offset of the screws' centers from the coupler ends.
hole_offset_from_end = 5.0;

module coupler_body() {
    rotate([0, 0, 180/8])
    cylinder(h = coupler_height, d = coupler_width, $fn = 8);
}

module halfcoupler_body() {
    translate([coupler_height/2 , 0, 0])
    difference() {
        rotate([0, -90, 0])
        coupler_body();
        translate([-2 * coupler_height, - coupler_width, -coupler_slot_width/2])
        cube([3 * coupler_height, 2 * coupler_width, 2 * coupler_width]);
    }
}

module clamping_screw() {
    union() {
        rotate([0, 0, 180/8])
        cylinder_outer(d = screw_hole_diameter, h = coupler_width, fn=8);
        translate([0, 0, -coupler_width])
        rotate([0, 0, 180/8])
        cylinder_outer(d = screw_head_diameter, h = coupler_width, fn=8);
    }
}

module clamping_nut() {
    union() {
        rotate([0, 0, 180/8])
        cylinder_outer(d = screw_hole_diameter, h = coupler_width, fn=8);
        translate([0, 0, -coupler_width])
        cylinder_outer(d = screw_nut_diameter, h = coupler_width, fn = 6);
    }
}

// a single bridging layer that higher layers rest upon

module single_layer_support() {
    intersection() {
        translate([-coupler_height/2, -coupler_width/2, -screw_head_to_nut/2 - eps1])
        cube([coupler_height, coupler_width, layer_thickness]);
        halfcoupler_body();
    }
}

// Make a V-shaped groove for leadscrew shaft to rest in
// This way there is always a width that fits, no matter printer tolerance

module coupler_leadscrew() {
    translate([coupler_height/2 - leadscrew_height, 0, 0])
    rotate([0, 90, 0])
    rotate([0, 0, 180/8])
    cylinder_outer(h = 2 * leadscrew_height, d = leadscrew_dia, fn = 8); // octagonal
}

module stepper_shaft() {
    translate([-coupler_height/2 - eps2, 0, 0])
    rotate([0, 90, 0])
    intersection() {
        rotate([0, 0, 180/8])
        cylinder_outer(h = stepper_shaft_height, d = stepper_shaft_dia, fn = 8);
        union() {
            translate([-stepper_shaft_dia/2, -stepper_shaft_dia/2, 0])
            cube([stepper_shaft_dia, stepper_shaft_dia, stepper_shaft_base_height]);
            translate([-stepper_shaft_width/2, -stepper_shaft_dia/2, 0])
            cube([stepper_shaft_width, stepper_shaft_dia, stepper_shaft_height]);
        }
    }
}


/*
// Old version:
// Circular holes for leadscrew and stepper shaft.

module coupler_leadscrew() {
    translate([coupler_height/2 - leadscrew_height, 0, 0])
    rotate([0, 90, 0])
    cylinder(h = 2 * leadscrew_height, d = leadscrew_dia); // round
}

module stepper_shaft() {
    translate([-coupler_height/2 - eps2, 0, 0])
    rotate([90, 0, 0])
    rotate([0, 90, 0]) {
        translate([0, 0, -eps1])
        cylinder(h = stepper_shaft_base_height + eps2 , d = stepper_shaft_dia);
        intersection() {
            cylinder(h = stepper_shaft_height , d = stepper_shaft_dia);
            translate([-stepper_shaft_dia/2, -stepper_shaft_width/2, stepper_shaft_base_height])
            cube([stepper_shaft_dia, stepper_shaft_width, stepper_shaft_height]);
        }
    }
}

*/

module halfcoupler() {
    difference() {
        union() {
            difference() {
                halfcoupler_body();
                translate([coupler_height/2 - hole_offset_from_end, hole_offset_from_center, -screw_head_to_nut/2 ])
                clamping_nut();
                translate([-coupler_height/2 + hole_offset_from_end, hole_offset_from_center, -screw_head_to_nut/2])
                clamping_nut();
                translate([coupler_height/2 - hole_offset_from_end, -hole_offset_from_center, -screw_head_to_nut/2])
                clamping_screw();
                translate([-coupler_height/2 + hole_offset_from_end, -hole_offset_from_center, -screw_head_to_nut/2])
                clamping_screw();
            }
            single_layer_support();
        }
        coupler_leadscrew();
        stepper_shaft();
    }
}

/* make cutout */

module cutout(cut = true) {
    if (cut)
        difference() {
            children();
            translate([-100, -200, -100])
            cube([200, 200, 200]);
        }
    else
        children();
}

// model of an assembled shaft coupler in the motor mount cavity
// to check everything fits

module assembly() {
    // cavity in motor mount
    cavity_height = 28;
    cavity_diameter = 22;
    %translate([-cavity_height/2, 0, 0])
    rotate([0, 90, 0])
    difference() {
        translate([-cavity_diameter, -cavity_diameter, 0])
        cube([2 * cavity_diameter, 2 * cavity_diameter,  cavity_height]);
        translate([0, 0, -cavity_height/2])
        cylinder(h = cavity_height * 2, d = cavity_diameter);
    }

    // motor shaft
    shaft_dia = 5.0;
    shaft_height = 10;
    shaft_width = 3.0;
    shaft_base_height = 3.5;
    translate([-coupler_height/2 - 0.1, 0, 0])
    rotate([0, 90, 0])
    color("Gray")
    intersection() {
        cylinder(h = shaft_height, d = shaft_dia);
        union() {
            translate([-shaft_dia/2, -shaft_dia/2, 0])
            cube([shaft_dia, shaft_dia, shaft_base_height]);
            translate([-shaft_width/2, -shaft_dia/2, 0])
            cube([shaft_width, shaft_dia, shaft_height]);
        }
    }

    // leadscrew
    color("Gray")
    translate([coupler_height/2 - leadscrew_height + 0.1, 0, 0])
    rotate([0, 90, 0])
    cylinder(h = coupler_height, d = 4.0);

    cutout() {
        // clamping screws
        delta_x = coupler_height/2 - hole_offset_from_end;
        delta_y = hole_offset_from_center;
        for (x = [delta_x, -delta_x])
        for (y = [delta_y, -delta_y])
        mirror([0, 0, y>0?1:0])
        translate([x, y, 0]) {
            translate([0, 0, -screw_head_to_nut/2])
            mirror([0, 0, 1])
            screw(M3_pan_screw, 10);
            translate([0, 0, screw_head_to_nut/2])
            nut(M3_nut);
        }


        // two halfcouplers
        rotate([180, 0, 0])
        halfcoupler();
        halfcoupler();
    }
}

// choose between printer-ready halfcoupler and assembled model.

if (true) {
    translate([0, 0, coupler_inradius])
    halfcoupler();
}
else {
    assembly();
};

// not truncated

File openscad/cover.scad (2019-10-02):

// pcb cover
// needs more aesthetics.

$fn = 120;
eps1 = 0.001;
slack = 0.4; // slack around components
wall_thickness = 2.0;
cover_height = 8.0;
pcb_thickness = 1.6;
pcb_size_x = 40;
pcb_size_y = 30;

// hole for pinheader. parameters are number of rows, number of columns.

module pinheader(row, col) {
    pitch = 2.54;
    translate(- [pitch/2, pitch/2])
    square([row * pitch, col * pitch]);
}

// hole for pushbutton knob.

module button() {
    circle(d = 3.5);
}

// hole for led.

module led() {
    square([2, 1.25], true);
}

module corner_side() {
    hull() {
        cube([wall_thickness, 2 * wall_thickness, eps1]);
        translate([0, 0, cover_height])
        cube([wall_thickness, cover_height + 2 * wall_thickness, eps1]);
    }
}

module corner() {
    translate([0, -wall_thickness, 0])
    corner_side();
    translate([wall_thickness, -wall_thickness, 0])
    rotate([0, 0, 90])
    corner_side();
    translate([-wall_thickness, 0, pcb_thickness])
    cube([wall_thickness, wall_thickness, cover_height - pcb_thickness]);
}

module corners() {
    rotate([0, 0, 270])
    corner();
    translate([pcb_size_x, 0, 0])
    rotate([0, 0, 0])
    corner();
    translate([0, pcb_size_y, 0])
    rotate([0, 0, 180])
    corner();
    translate([pcb_size_x, pcb_size_y, 0])
    rotate([0, 0, 90])
    corner();    
}

module cover() {
    translate([0, 0, cover_height])
    difference() {
        translate([-wall_thickness, -wall_thickness, 0])
        cube([pcb_size_x + 2 * wall_thickness, pcb_size_y + 2 * wall_thickness, wall_thickness]);
        translate([0, 0, -1])
        linear_extrude(height = 10) 
        offset(r  =  slack) { 
            // positioning data from .drl drill file 
            translate(([21.36, 6.58]+[27.86, 2.08])/2) button(); // 4 pushbuttons
            translate(([11.708, 6.58]+[18.208, 2.08])/2) button();
            translate(([31.012, 6.58]+[37.512, 2.08])/2)  button();
            translate(([2.056, 6.58]+[8.556, 2.08])/2) button();
            translate([28.98, 10.644]) pinheader(3, 2);  // icp
            translate([15.772, 28.043]) pinheader(5, 1); // stepper
            translate([34.06, 17.248]) pinheader(1, 4);  // oled. XXX add support for oled screen
            translate([37.87, 12.168]) pinheader(1, 6);  // ext vertical header
            translate([34.06, 12.168]) pinheader(2, 6);  // dummy header, to avoid thin slivers
            
            
            // positioning data from .pos pick-and-place file 
            translate([30.377, 27.916]) led(); // led
        }
    }
    corners();
}

// choose between ready-to-print cover, and assembly of cover and pcb.
if (false) {
    // cover, positioned for fdm printing
    translate([pcb_size_x + wall_thickness, wall_thickness, cover_height + pcb_thickness])
    rotate([0, 180, 0])
    cover();
}
else {
    // assembly of cover and pcb
    cover();
 
    //   Flow to generate .stl file of pcb:
    // - In kicad: In pcbnew: File... Export... STEP
    // - In FreeCad: 
    // File... Open ... (select file exported from kicad)
    // Edit... Select All
    // File... Export... STL

    color("LimeGreen")
    import("paste_dispenser.stl", convexity=20);
}
    
// not truncated

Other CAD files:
openscad/aerzetix-C19143/insert_practice.stl
openscad/mcmaster-94180A353/plunger_tip.stl
openscad/mcmaster-94180A353/syringe_holder.stl
openscad/mcmaster-94180A353/plunger.stl
openscad/mcmaster-94180A353/coupler.stl
openscad/mcmaster-94180A353/motor_mount.stl
openscad/mcmaster-94180A353/insert_practice.stl
openscad/insert_practice.scad
openscad/attic/coupler.scad
openscad/lid.scad
openscad/m4_threaded_insert.scad
openscad/pcb.scad
openscad/plunger.scad
openscad/util.scad

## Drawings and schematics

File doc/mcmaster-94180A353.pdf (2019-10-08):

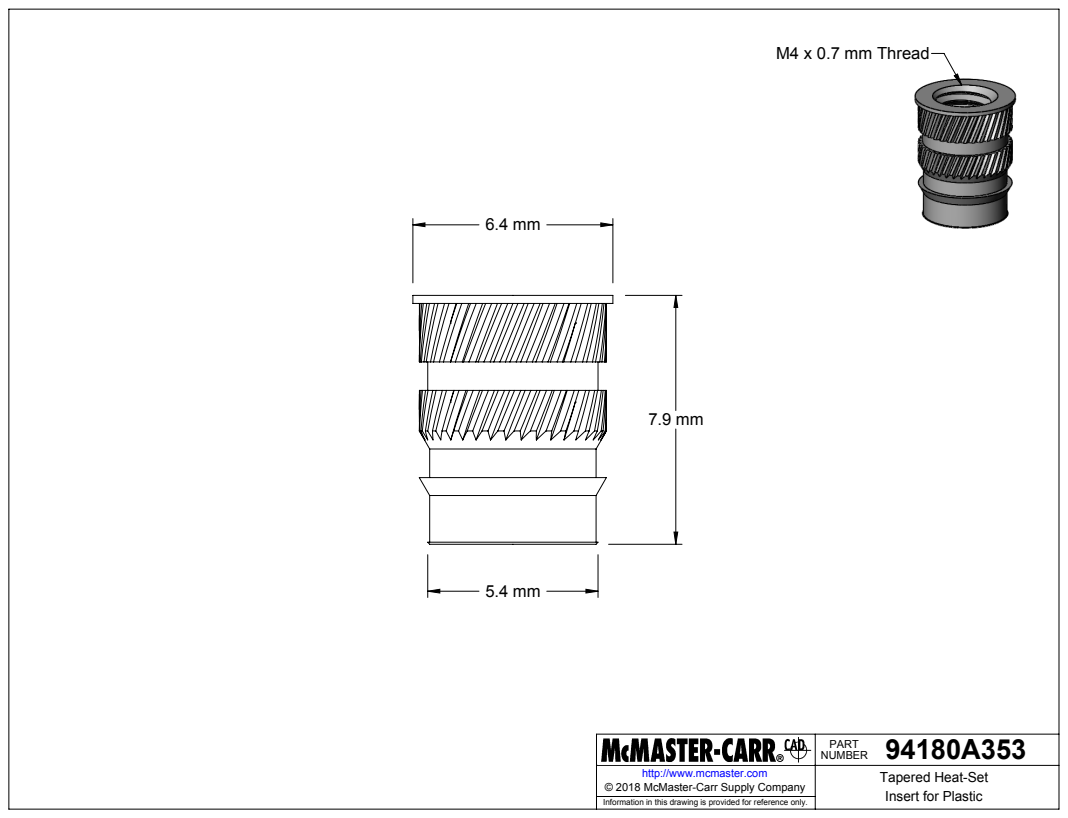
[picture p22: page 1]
M4 x 0.7 mm Thread

94180A353 PART NUMBER

http://www.mcmaster.com | Tapered Heat-Set Insert for Plastic © 2018 McMaster-Carr Supply Company

Information in this drawing is provided for reference only.

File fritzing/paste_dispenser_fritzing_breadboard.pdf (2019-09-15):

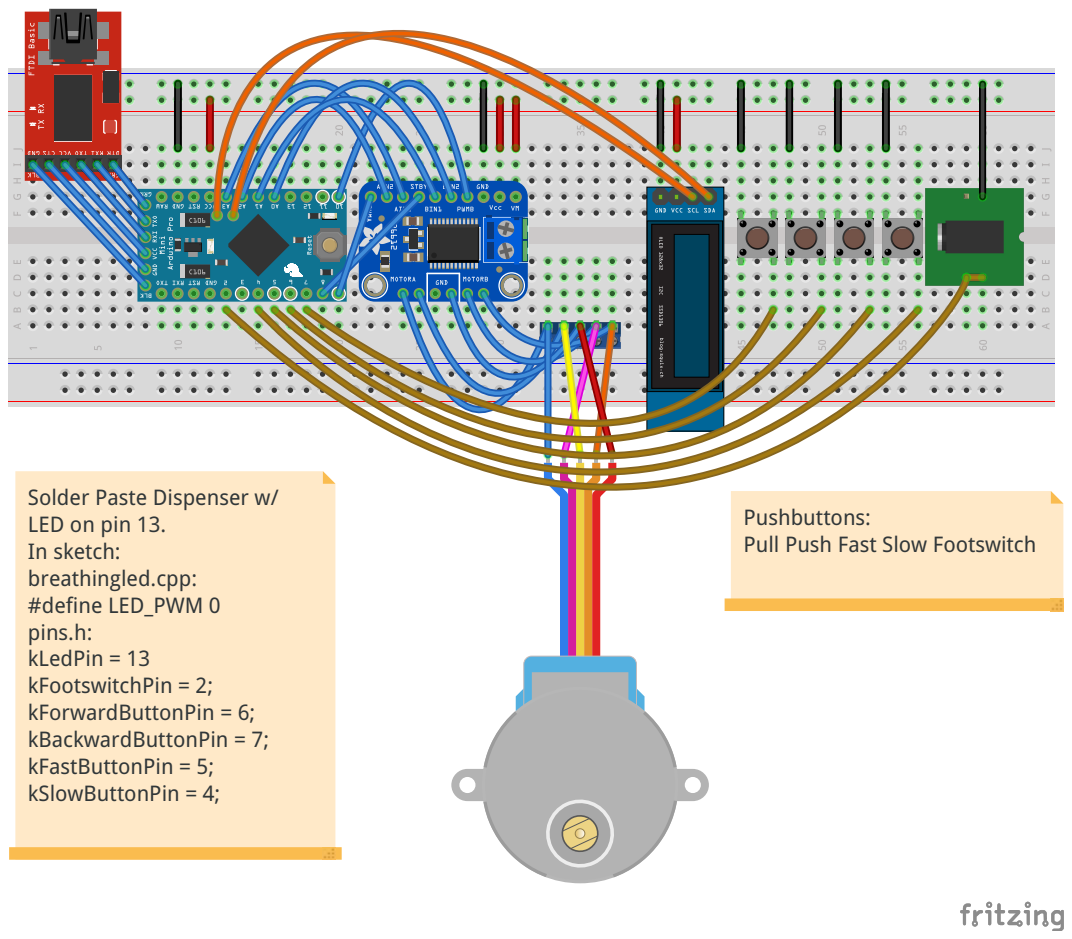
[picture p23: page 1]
Slo; wit; old; Dis; pin; p: #define LED_PWM; s.h: kLedPin; Pin

s: Pull Push Fas

3. In sketch: breathingled.c

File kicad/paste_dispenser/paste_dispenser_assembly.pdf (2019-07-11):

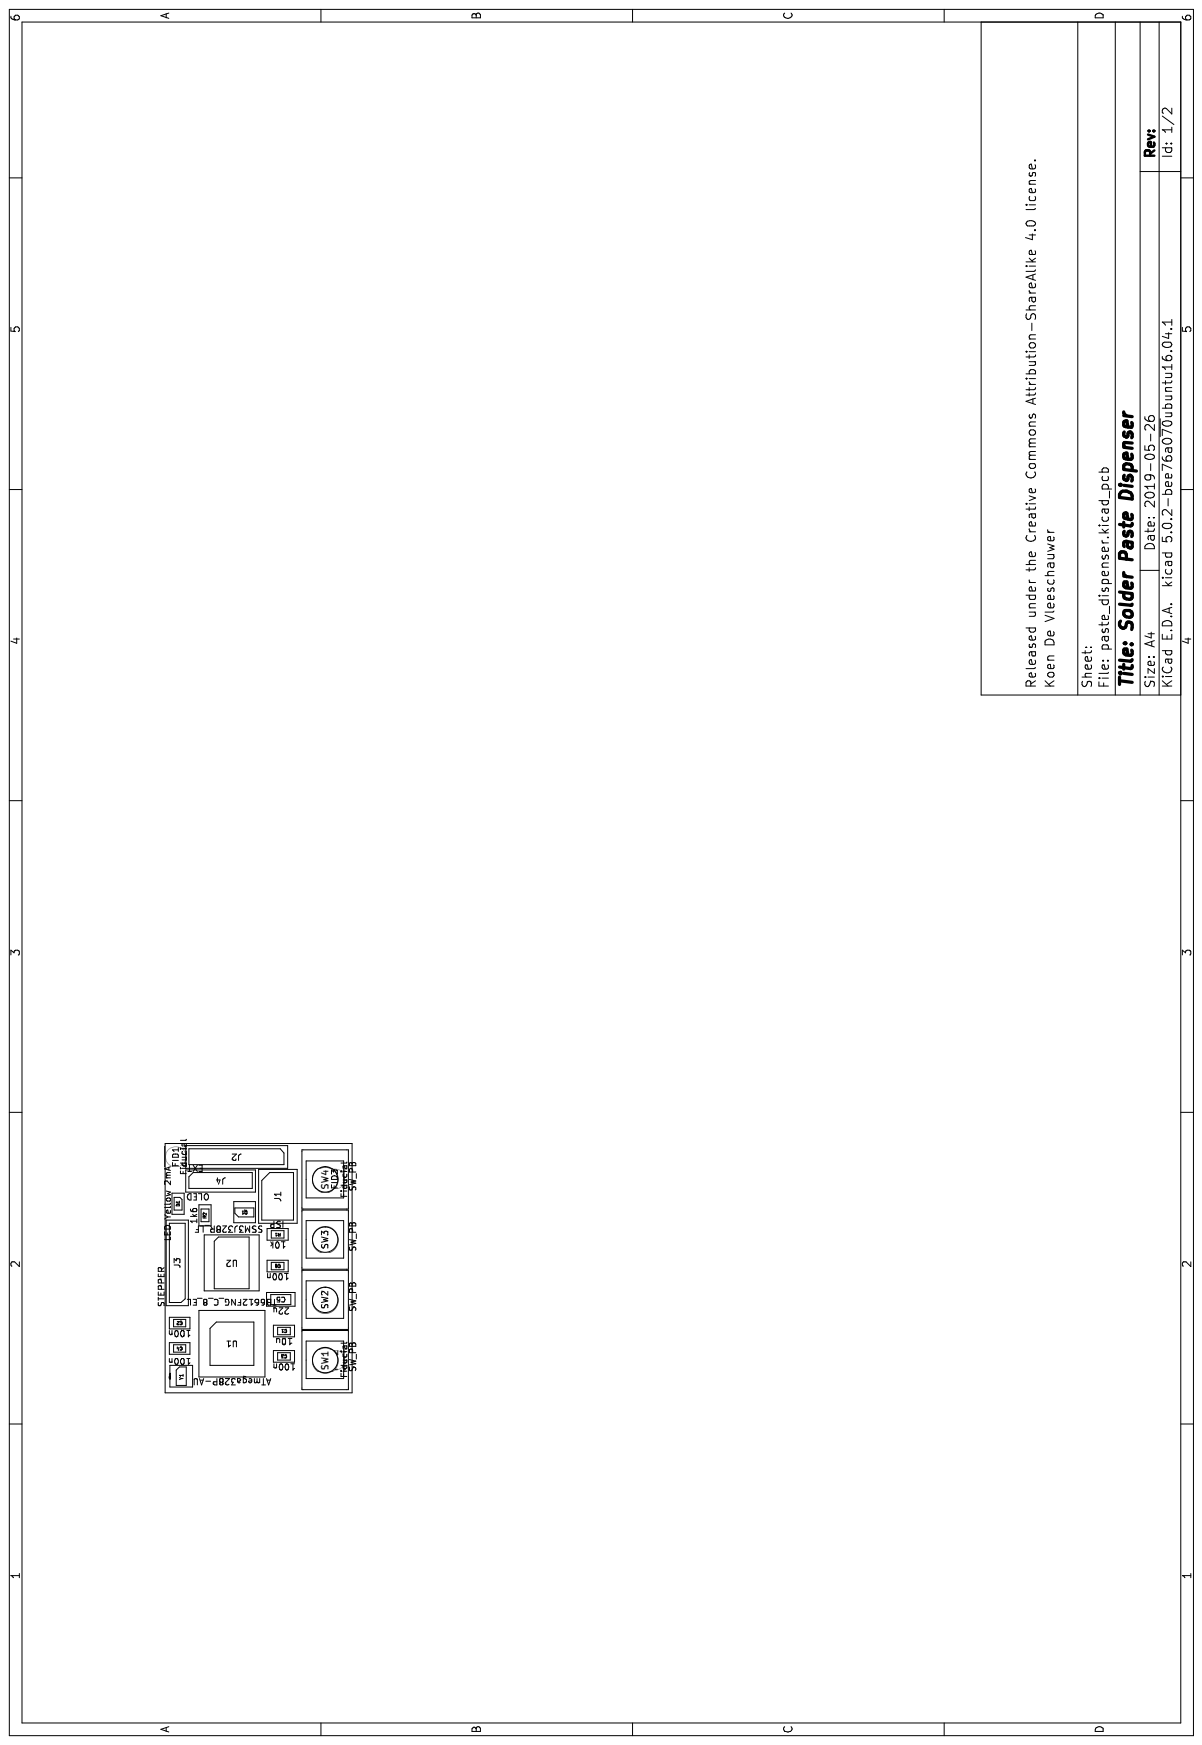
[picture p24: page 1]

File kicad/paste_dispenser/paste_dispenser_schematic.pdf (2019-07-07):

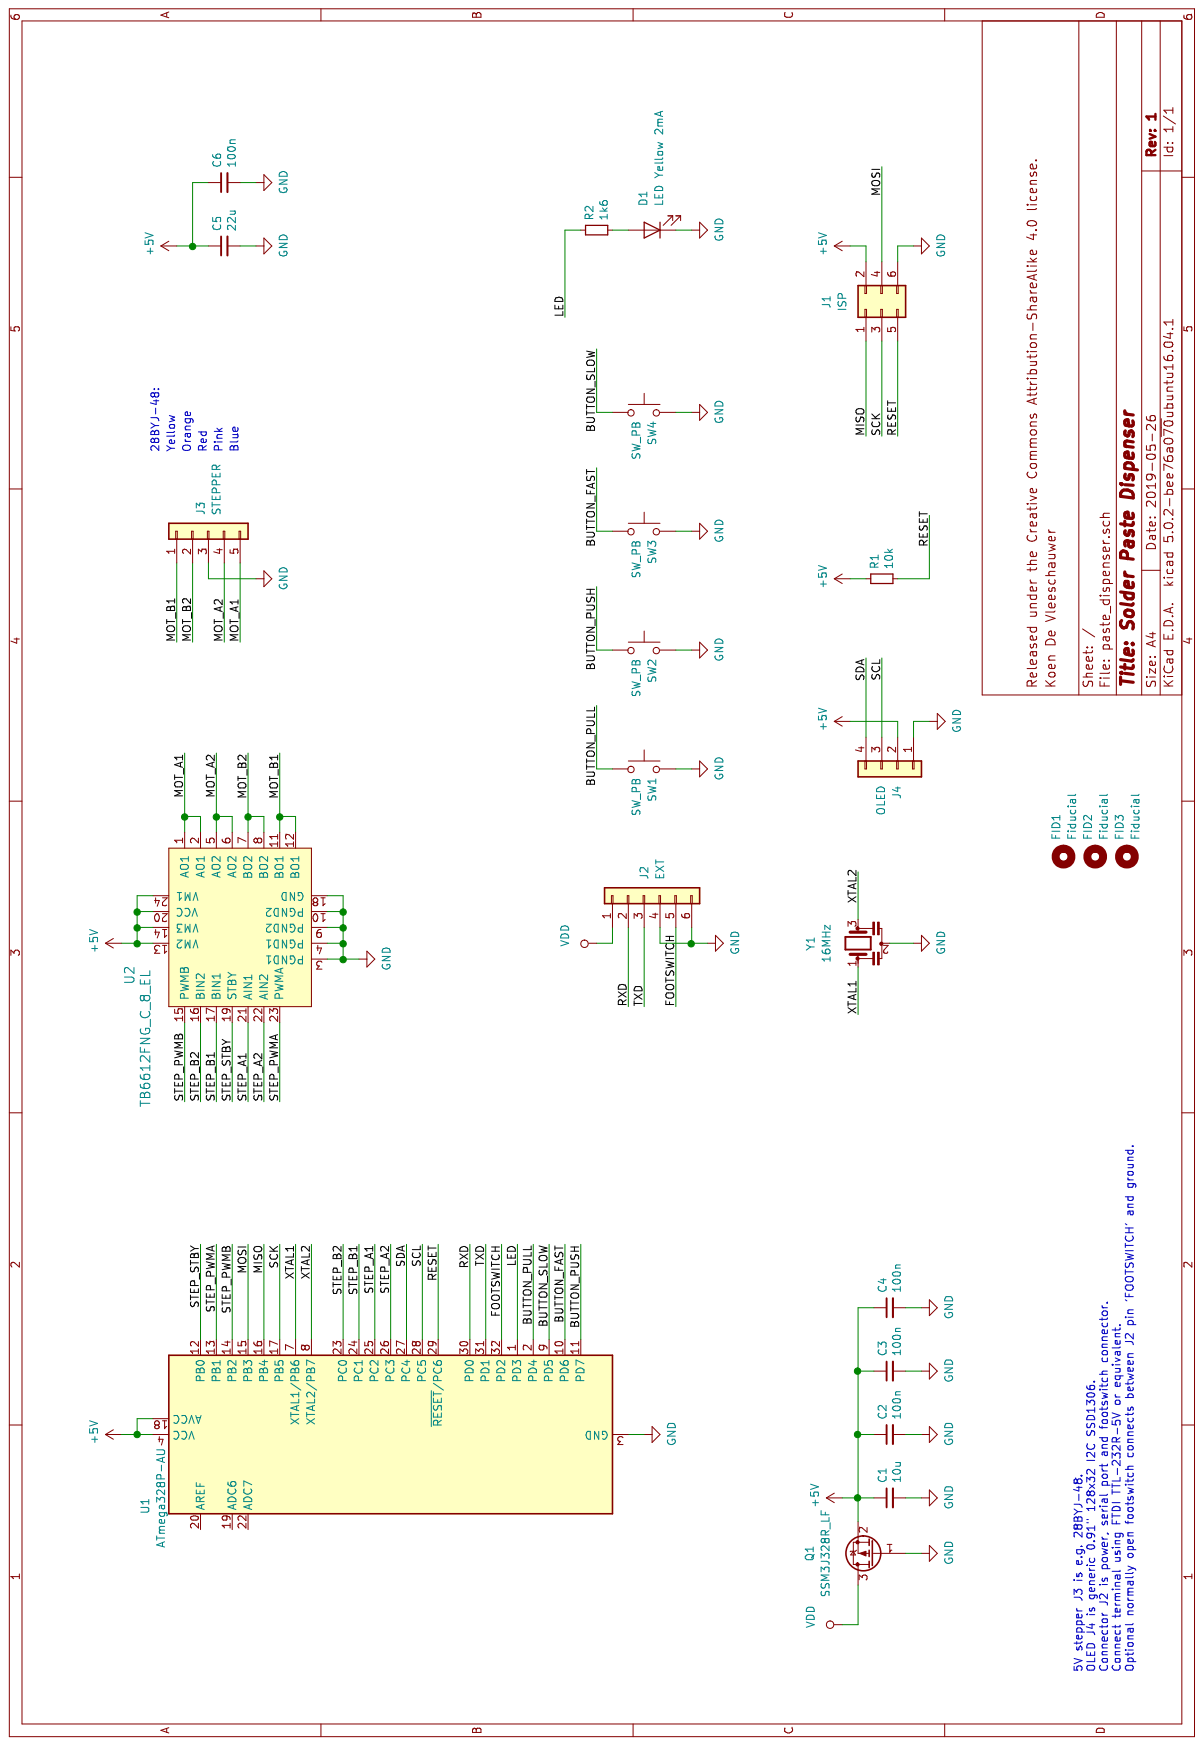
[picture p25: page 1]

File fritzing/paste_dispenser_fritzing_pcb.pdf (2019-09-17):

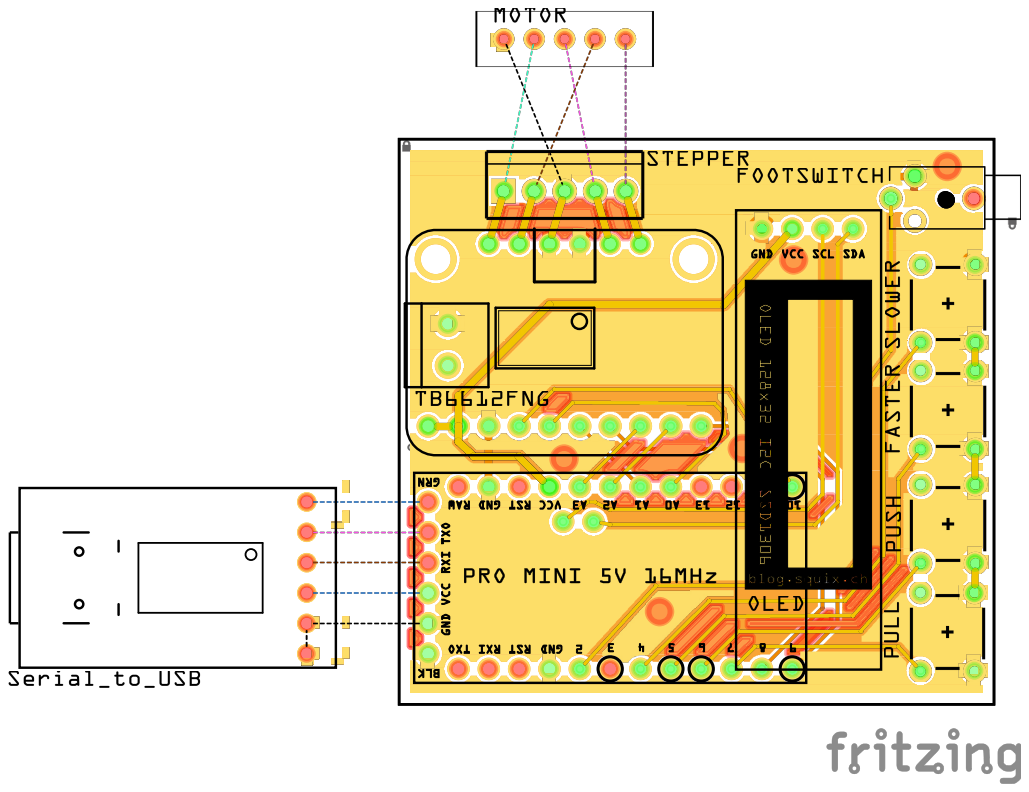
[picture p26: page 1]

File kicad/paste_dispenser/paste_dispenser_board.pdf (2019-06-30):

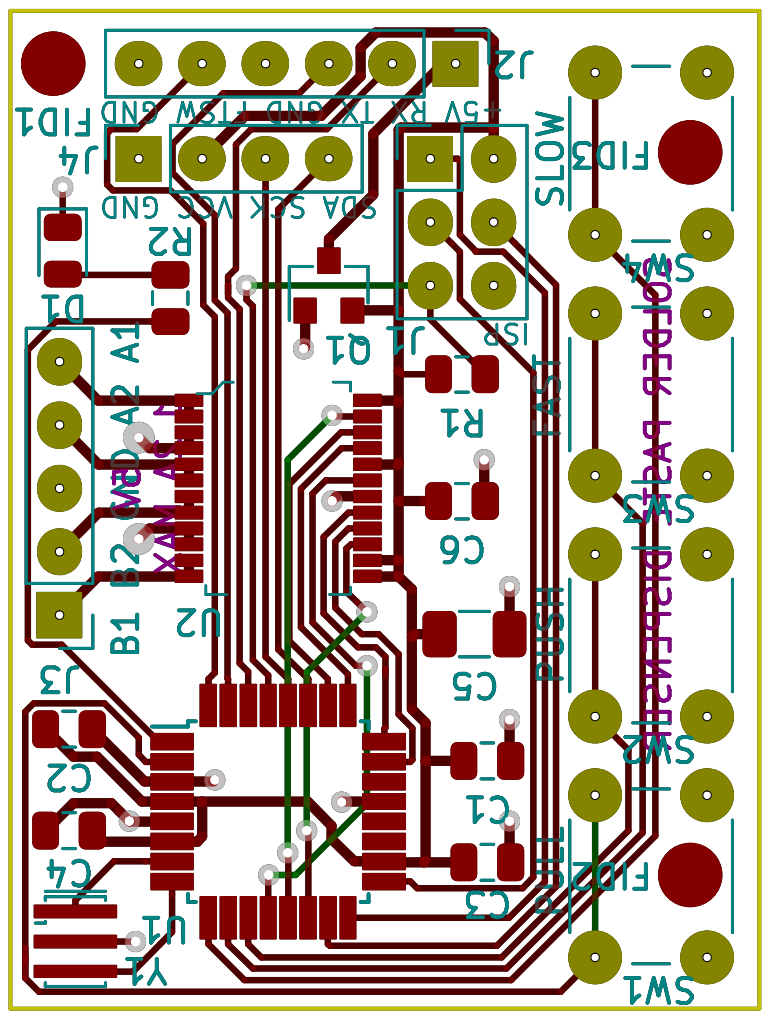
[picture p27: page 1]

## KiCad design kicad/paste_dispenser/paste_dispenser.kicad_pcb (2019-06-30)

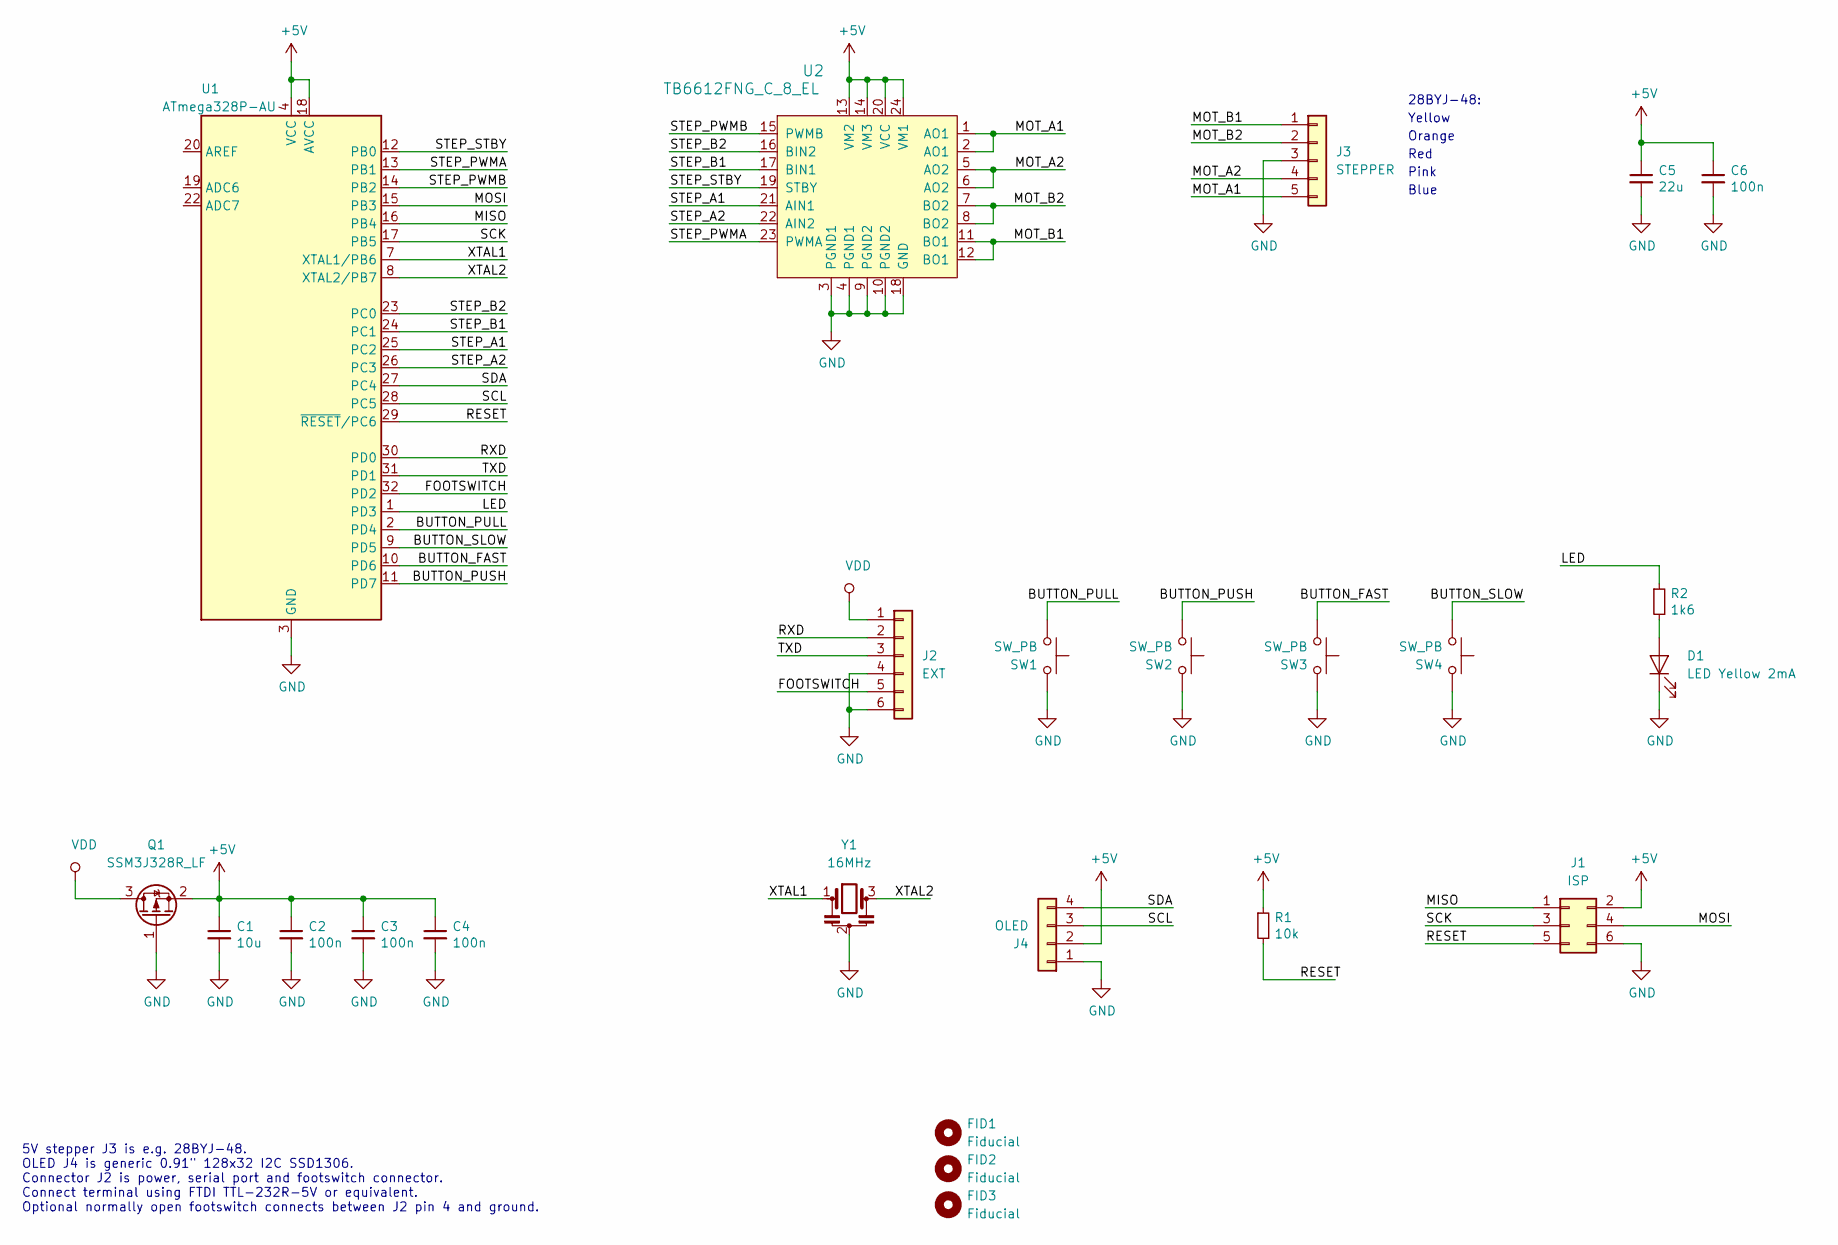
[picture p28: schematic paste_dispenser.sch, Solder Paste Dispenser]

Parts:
C1: 10u; C_0805_2012Metric; Manufacturer Part No CC805KKX5R7BB106
C2, C3, C4, C6: 100n; C_0805_2012Metric; Manufacturer Part No CC805KRX7R7BB104
C5: 22u; C_1206_3216Metric; Manufacturer Part No EMK316BB7226ML-T
D1: LED Yellow 2mA; LED_0805_2012Metric; Manufacturer Part No APTD2012LSYCK
FID1, FID2, FID3: Fiducial; Fiducial_1mm_Dia_2.54mm_Outer_CopperTop
J1: ISP; PinHeader_2x03_P2.54mm_Vertical; Manufacturer Part No 2822
J2: EXT; PinHeader_1x06_P2.54mm_Vertical; Manufacturer Part No 70553-0005
J3: STEPPER; PinHeader_1x05_P2.54mm_Vertical; Manufacturer Part No DNP
J4: OLED; PinSocket_1x04_P2.54mm_Vertical; Manufacturer Part No M20-7820442
Q1: SSM3J328R_LF; SOT-23; Manufacturer Part No SSM3J328R,LF
R1: 10k; R_0805_2012Metric; Manufacturer Part No AC0805FR-0710KL
R2: 1k6; R_0805_2012Metric; Manufacturer Part No AC0805FR-071K6L
SW1, SW2, SW3, SW4: SW_PB; SW_PUSH_6mm; Manufacturer Part No B3F-1000
U1: ATmega328P-AU; TQFP-32_7x7mm_P0.8mm; Manufacturer Part No ATMEGA328P-AU
U2: TB6612FNG_C_8_EL; LSSOP-24_W5.6mm; Manufacturer Part No TB6612FNG,C,8,EL
Y1: 16MHz; Resonator_SMD_muRata_CSTxExxV-3Pin_3.0x1.1mm_HandSoldering; Manufacturer Part No CSTNE16M0V530000R

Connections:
+5V: C1.1, C2.1, C3.1, C4.1, C5.1, C6.1, J1.2, J4.2, Q1.2 (S), R1.1, U1.4 (VCC), U1.6 (VCC), U1.18 (AVCC), U2.13 (VM2), U2.14 (VM3), U2.20 (VCC), U2.24 (VM1)
/BUTTON_FAST: SW3.1, U1.10 (PD6)
/BUTTON_PULL: SW1.1, U1.2 (PD4)
/BUTTON_PUSH: SW2.1, U1.11 (PD7)
/BUTTON_SLOW: SW4.1, U1.9 (PD5)
/FOOTSWITCH: J2.5, U1.32 (PD2)
/LED: R2.1, U1.1 (PD3)
/MISO: J1.1, U1.16 (PB4)
/MOSI: J1.4, U1.15 (PB3)
/MOT_A1: J3.5, U2.1 (AO1), U2.2 (AO1)
/MOT_A2: J3.4, U2.5 (AO2), U2.6 (AO2)
/MOT_B1: J3.1, U2.11 (BO1), U2.12 (BO1)
/MOT_B2: J3.2, U2.7 (BO2), U2.8 (BO2)
/RESET: J1.5, R1.2, U1.29 (~RESET~/PC6)
/RXD: J2.2, U1.30 (PD0)
/SCK: J1.3, U1.17 (PB5)
/SCL: J4.3, U1.28 (PC5)
/SDA: J4.4, U1.27 (PC4)
/STEP_A1: U1.25 (PC2), U2.21 (AIN1)
/STEP_A2: U1.26 (PC3), U2.22 (AIN2)
/STEP_B1: U1.24 (PC1), U2.17 (BIN1)
/STEP_B2: U1.23 (PC0), U2.16 (BIN2)
/STEP_PWMA: U1.13 (PB1), U2.23 (PWMA)
/STEP_PWMB: U1.14 (PB2), U2.15 (PWMB)
/STEP_STBY: U1.12 (PB0), U2.19 (STBY)
/TXD: J2.3, U1.31 (PD1)
/XTAL1: U1.7 (XTAL1/PB6), Y1.1
/XTAL2: U1.8 (XTAL2/PB7), Y1.3
GND: C1.2, C2.2, C3.2, C4.2, C5.2, C6.2, D1.1 (K), J1.6, J2.4, J2.6, J3.3, J4.1, Q1.1 (G), SW1.2, SW2.2, SW3.2, SW4.2, U1.3 (GND), U1.5 (GND), U1.21 (GND), U2.3 (PGND1), U2.4 (PGND1), U2.9 (PGND2), U2.10 (PGND2), U2.18 (GND), Y1.2
unnamed: D1.2 (A), R2.2
VDD: J2.1, Q1.3 (D)

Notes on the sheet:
5V stepper J3 is e.g. 28BYJ-48. OLED J4 is generic 0.91" 128x32 I2C SSD1306. Connector J2 is power, serial port and footswitch connector. Connect terminal using FTDI TTL-232R-5V or equivalent. Optional normally open footswitch connects between J2 pin 4 and ground.
Yellow
Orange
Red
Pink
Blue
28BYJ-48:

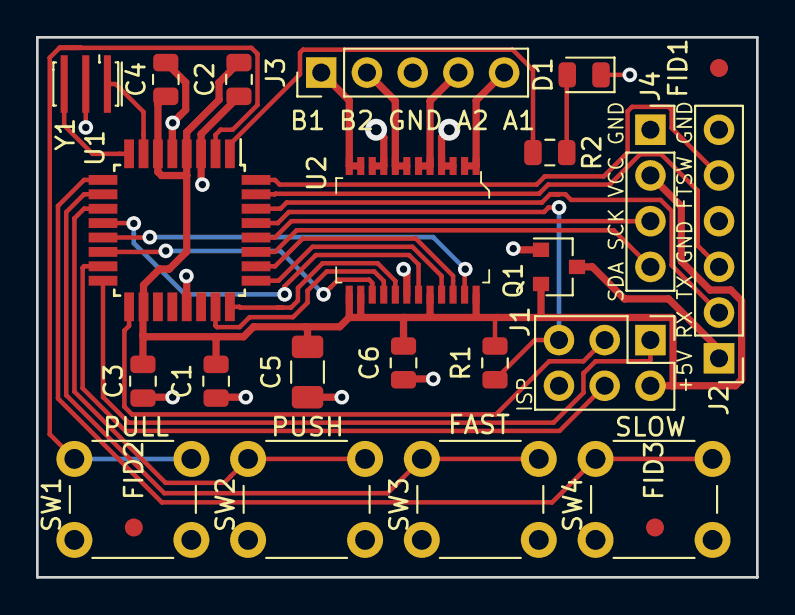
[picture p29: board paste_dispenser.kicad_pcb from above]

Board: 2 copper layers, 40.0 x 30.0 mm, 24 parts (0 on the bottom side), 31 nets.

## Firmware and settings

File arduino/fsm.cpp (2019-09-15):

#include "pins.h"
#include "settings.h"
#include "motor.h"
#include "buttons.h"
#include "breathing_led.h"
#include "oled.h"
#include "fsm.h"

//#define DEBUG 1

namespace fsm {
  
  static const long kIdleTimeoutMillis = 20000; // put motor and driver in standby after 20 seconds idle time.
  unsigned long idleTimeMillis = 0;

  static bool pulled_back = false; // True if previous motion ended in pullback
  static uint16_t dot_steps = 0; // Number of steps to take in single shot mode.

  static const uint8_t STATE_IDLE = 0;           // Waiting for work. If "forward" button pushed and forwardSteps is zero, move to STATE_FORWARD and make beads. If "forward" button pushed and forwardSteps is not zero, move to STATE_DOT_WAIT and make dots. 
  static const uint8_t STATE_FORWARD = 1;        // Making beads. Moving piston forward as long as "push" button is pressed.  
  static const uint8_t STATE_BACKWARD = 2;       // Withdrawing. Moving piston backward as long as "pull" button is pressed.
  static const uint8_t STATE_DOT_WAIT = 3;       // Making dots. "forward" button pressed. Wait for user to release the "forward" button. Then move to STATE_DOT and make dot.
  static const uint8_t STATE_DOT = 4;            // Making dots. Moving piston forward a configured number of steps.
  static const uint8_t STATE_PULLBACK_WAIT = 5;  // After forward movement, if pullbackSteps non-zero then wait for pullback timeout to expire. If user does not press "forward" or "backward" buttons before timeout, move to STATE_PULLBACK.
  static const uint8_t STATE_PULLBACK = 6;       // Pullback. Withdraw a configured number of steps, to stop oozing. 
  static const uint8_t STATE_SLEEP = 7;          // Waiting for work, but with the motor switched off.
  
  static uint8_t state = STATE_IDLE;

  void setup () {
    state = STATE_IDLE;
    return; 
  }

  bool sleeping() {
    return state == STATE_SLEEP;
  }

  inline bool forwardButtonPressed() {
    return buttons::isPressed[kForwardButtonPin] || buttons::isPressed[kFootswitchPin];
  }

  inline bool backwardButtonPressed() {
    return buttons::isPressed[kBackwardButtonPin];
  }

  static uint16_t steps_per_second = 0; 
  
  void motorOn(bool is_forward) {

    uint16_t new_steps_per_second = 0;
 
    if (is_forward) new_steps_per_second = settings::forwardSpeed;
    else new_steps_per_second = settings::backwardSpeed;

    if (new_steps_per_second != steps_per_second) {
      steps_per_second = new_steps_per_second;
      oled::print(steps_per_second);
    }

    motor::setSpeed(steps_per_second, is_forward); // move motor

    // have led blink faster when motor runs faster
    const uint16_t steps_to_led_ratio = settings::kMaxSpeed / 250;
    uint16_t led_period_millis = 500 - steps_per_second / steps_to_led_ratio; // faster than map(steps_per_second, 0, settings::kMaxSpeed, 500, 250);
    led_period_millis = constrain(led_period_millis, 100, 1000); // constrain to reasonable values
    breathingLed::blink(64, led_period_millis); // blink led

    return;
  }

  void motorOff() {
    motor::setSpeed(0, true);
    breathingLed::off();

    if (steps_per_second != settings::forwardSpeed) {
      steps_per_second = settings::forwardSpeed;
      oled::print(steps_per_second);
    }
    
    return;
  }

  void nextState(uint8_t new_state) {
    if (state == new_state) return;
#ifdef DEBUG
    switch(new_state) {
      case STATE_IDLE:
        Serial.println(F("STATE_IDLE"));
        break;
      case STATE_FORWARD:
        Serial.println(F("STATE_FORWARD"));
        break;
      case STATE_BACKWARD:
        Serial.println(F("STATE_BACKWARD"));
        break;
      case STATE_DOT_WAIT:
        Serial.println(F("STATE_DOT_WAIT"));
        break;  
      case STATE_DOT:
        Serial.println(F("STATE_DOT"));
        break;
      case STATE_PULLBACK_WAIT:
        Serial.println(F("STATE_PULLBACK_WAIT"));
        break; 
      case STATE_PULLBACK:
        Serial.println(F("STATE_PULLBACK"));
        break;     
      case STATE_SLEEP:
        Serial.println(F("STATE_SLEEP"));
        break;
      default:
        Serial.println(F("STATE ERROR"));
        break;  
    }
#endif
    state = new_state;
    if ((new_state == STATE_IDLE) || (new_state == STATE_PULLBACK_WAIT))  {
      idleTimeMillis = millis();
    }
  }
  
  void loop () {
    switch (state) {
      case STATE_PULLBACK_WAIT:
        if (millis() - idleTimeMillis > settings::pullbackDelay) {
          pulled_back = settings::forwardSteps != 0; // if working in "dot" mode increase number of steps to compensate for pullback
          motor::steps = 0;
          motorOn(false);
          nextState(STATE_PULLBACK);
          break;
        }
        pulled_back = false;
        // fallthrough to STATE_IDLE
      case STATE_IDLE:
        if (forwardButtonPressed()) {
          if (settings::forwardSteps == 0) {
            motorOn(true);
            nextState(STATE_FORWARD);
          } else {
            breathingLed::on();
            nextState(STATE_DOT_WAIT);
          }
        } else if (backwardButtonPressed()) {
          motorOn(false);
          nextState(STATE_BACKWARD);
        } else if (millis() - idleTimeMillis > kIdleTimeoutMillis) {
          motor::sleep(); // put driver in standby
          oled::clear(); // clear display to avoid burn-in
          breathingLed::breathe();
          nextState(STATE_SLEEP);
        } else if (steps_per_second != settings::forwardSpeed) { // updating display is low priority
          steps_per_second = settings::forwardSpeed;
          oled::print(steps_per_second);
        }
        break;
      case STATE_FORWARD:
        if (!forwardButtonPressed()) {
          motorOff();
          if (settings::pullbackSteps != 0) nextState(STATE_PULLBACK_WAIT);
          else nextState(STATE_IDLE);
        }
        // Handle speed changes
        if (steps_per_second != settings::forwardSpeed) motorOn(true);
        break;
      case STATE_BACKWARD:
        if (!backwardButtonPressed()) {
          motorOff();
          nextState(STATE_IDLE);
        }
        break;
      case STATE_DOT_WAIT:
        if (!forwardButtonPressed()) { // wait for button release
          // if previous forward motion ended in pullback, add pullbackSteps to the number of steps to do.
          // This keeps the amount of paste dispensed the same, whether pullback happened or not.
          dot_steps = settings::forwardSteps;
          if (pulled_back) dot_steps += settings::pullbackSteps;
          pulled_back = false; 
          motor::steps = 0;
          motorOn(true);
          nextState(STATE_DOT);  
        }
        break;
      case STATE_DOT:
        if (motor::steps >= dot_steps) {
          motorOff();
          if (settings::pullbackSteps != 0) nextState(STATE_PULLBACK_WAIT);
          else nextState(STATE_IDLE);
        }
        break;   
      case STATE_PULLBACK:
        if (motor::steps >= settings::pullbackSteps) {
          motorOff();
          nextState(STATE_IDLE); 
        }
        break;  
      case STATE_SLEEP:
        // wake up if user is pushing buttons or configuring using the serial console
        if (forwardButtonPressed() || backwardButtonPressed() || buttons::isPressed[kSlowButtonPin] || buttons::isPressed[kFastButtonPin] || (steps_per_second != settings::forwardSpeed)) {
          motor::wakeup(); // wake up driver
          oled::print(steps_per_second); // wake up display
          breathingLed::off();
          nextState(STATE_IDLE);
        }
        break;
      default:
        nextState(STATE_IDLE);
        break;
    }
  }
}
// not truncated

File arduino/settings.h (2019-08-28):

#ifndef SETTINGS_H
#define SETTINGS_H

namespace settings {

  static const uint8_t kMaxProfile = 4; // 5 profiles, numbered 0..4
  static const uint16_t kMaxSpeed = 800;
  static const uint16_t kDefaultSpeed = 300;
  static const uint16_t kMaxPullbackDelay = 10000;
  static const uint16_t kMaxSteps = 10000;
  static const uint16_t kMaxMicrosteps = 64;
  static const uint16_t kDefaultMicrosteps = 2;

  extern uint16_t profileNumber; // current profile
  extern uint16_t forwardSpeed; // speed when forward button is pressed.
  extern uint16_t forwardSteps; // number of steps to move when forward button is pressed. if 0 keep moving until forward button is released.
  extern uint16_t backwardSpeed; // speed when backward button is pressed
  extern uint16_t pullbackDelay; // time to wait after forward motion before pulling back. in milliseconds.
  extern uint16_t pullbackSteps; // number of steps to pull back. if 0 don't pull back.
  extern uint16_t microSteps; // microsteps per full step. valid values are 1, 2, 4, 5, 16, 32, 64.

  void writeConfig(); // writes current profile and profile number to eeprom.
  void readConfig(); // reads profile and profile number from eeprom.
  void readchar(); // read one character from the serial port
  
  extern void setup();
  extern void loop();
}

#endif

// not truncated

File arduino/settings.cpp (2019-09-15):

#include <Arduino.h>
#include <EEPROMWearLevel.h>
#include "pins.h"
#include "buttons.h"
#include "settings.h"
#include "fsm.h"
#include "motor.h"

// Change EEPROM_LAYOUT_VERSION when number of indexes changed etc.

#define EEPROM_LAYOUT_VERSION 1
#define EEPROM_INDEXES 1
#define EEPROM_INDEX_STORED_PROFILE 0

#define EEPROM_MAGIC_NUMBER 0xdeadbeef

namespace settings {

  /*
   * Button state
   */
  static long kButtonAutoRepeat = 500; /* milliseconds */

  static const uint8_t BUTTON_IDLE = 0;  // Waiting for work.
  static const uint8_t BUTTON_FAST = 1;  // "fast" button pressed. Increase speed.
  static const uint8_t BUTTON_SLOW = 2;  // "slow" button pressed. Decrease speed.

  static uint8_t button_state = BUTTON_IDLE;
  static bool restoreProfileNumber = true; // restore profileNumber at startup

  /*
   * active profile
   */

  uint32_t magicNumber; // check if saved settings are valid
  uint16_t profileNumber; // current profile
  uint16_t forwardSpeed; // speed when forward button is pressed.
  uint16_t forwardSteps; // number of steps to move when forward button is pressed. if 0 keep moving until forward button is released (default).
  uint16_t backwardSpeed; // speed when backward button is pressed. default 500.
  uint16_t pullbackDelay; // time to wait after forward motion before pulling back. in milliseconds.
  uint16_t pullbackSteps; // number of steps to pull back. if 0 don't pull back (default).
  uint16_t microSteps; // microsteps per full step. valid values are 1, 2, 4, 5, 16, 32, 64.

  /*
   * profiles as saved in eeprom
   */

  typedef struct  {
    uint32_t magicNumber;
    uint8_t profileNumber; // default profile to use at next boot
    uint16_t forwardSpeed[kMaxProfile+1];
    uint16_t forwardSteps[kMaxProfile+1];
    uint16_t backwardSpeed[kMaxProfile+1];
    uint16_t pullbackDelay[kMaxProfile+1];
    uint16_t pullbackSteps[kMaxProfile+1];
    uint16_t microSteps[kMaxProfile+1];
  } profile;

  /*
   * enforce valid values in profile
   */

  void constrainConfig() {
    profileNumber = constrain(profileNumber, 0, kMaxProfile);
    forwardSpeed = constrain(forwardSpeed, 1, kMaxSpeed);
    forwardSteps = constrain(forwardSteps, 0, kMaxSteps);
    backwardSpeed = constrain(backwardSpeed, 1, kMaxSpeed);
    pullbackDelay = constrain(pullbackDelay, 0, kMaxPullbackDelay);
    pullbackSteps = constrain(pullbackSteps, 0, kMaxSteps);
    microSteps = constrain(microSteps, 1, kMaxMicrosteps);
    if ((microSteps != 1) && (microSteps != 2) && (microSteps != 4) && (microSteps != 8) && (microSteps != 16) && (microSteps != 32)  && (microSteps != 64)) microSteps = 2; // valid values for microstepping
    return;
  }

  /*
   * save current profile to eeprom
   */
  
  void writeConfig() {
    profile storedProfile;
    constrainConfig(); // make certain we write valid values
    EEPROMwl.get(EEPROM_INDEX_STORED_PROFILE, storedProfile);
    storedProfile.magicNumber = EEPROM_MAGIC_NUMBER;
    storedProfile.profileNumber = profileNumber;
    storedProfile.forwardSpeed[profileNumber] = forwardSpeed;
    storedProfile.forwardSteps[profileNumber] = forwardSteps;
    storedProfile.backwardSpeed[profileNumber] = backwardSpeed;
    storedProfile.pullbackDelay[profileNumber] = pullbackDelay;
    storedProfile.pullbackSteps[profileNumber] = pullbackSteps;
    storedProfile.microSteps[profileNumber] = microSteps;
    EEPROMwl.put(EEPROM_INDEX_STORED_PROFILE, storedProfile);
    return;
  }

  // restoreProfileNumber = false:  read profile only, keep profileNumber unchanged
  // restoreProfileNumber = true: read both profile and profileNumber 
  void readConfig() {
    profile storedProfile;
    uint16_t storedProfileNumber;
    EEPROMwl.get(EEPROM_INDEX_STORED_PROFILE, storedProfile);
    if (storedProfile.magicNumber != EEPROM_MAGIC_NUMBER) { // eeprom corrupted or uninitialized
      storedProfile.magicNumber = EEPROM_MAGIC_NUMBER;
      storedProfile.profileNumber = 0;
      for (uint8_t i=0; i <= kMaxProfile; i++) {
        storedProfile.forwardSpeed[i] = kDefaultSpeed;
        storedProfile.forwardSteps[i] = 0;
        storedProfile.backwardSpeed[i] = kDefaultSpeed;
        storedProfile.pullbackDelay[i] = 0;
        storedProfile.pullbackSteps[i] = 0;
        storedProfile.microSteps[i] = kDefaultMicrosteps;
      }
      Serial.println(F("eeprom init"));
      EEPROMwl.put(EEPROM_INDEX_STORED_PROFILE, storedProfile);
    }
    if (restoreProfileNumber) {
      // restore profileNumber at startup
      profileNumber = storedProfile.profileNumber;
      restoreProfileNumber = false;
    }
    profileNumber = constrain(profileNumber, 0, kMaxProfile); // make certain profile number sane
    forwardSpeed = storedProfile.forwardSpeed[profileNumber];
    forwardSteps = storedProfile.forwardSteps[profileNumber];
    backwardSpeed = storedProfile.backwardSpeed[profileNumber];
    pullbackDelay = storedProfile.pullbackDelay[profileNumber];
    pullbackSteps = storedProfile.pullbackSteps[profileNumber];
    microSteps = storedProfile.microSteps[profileNumber];
    constrainConfig(); // make certain we have valid values
    motor::setMicrosteps(microSteps); // update microstep settings in stepper driver
    return;
  }

  /*
   * Buttons!
   */

  inline bool fastButtonPressed() {
    return buttons::isPressed[kFastButtonPin];
  }

  inline bool slowButtonPressed() {
    return buttons::isPressed[kSlowButtonPin];
  }

  void changeSpeed(int16_t delta) {
    int16_t newSpeed = forwardSpeed + delta;
    forwardSpeed = constrain(newSpeed, 1, kMaxSpeed);
  }

  void setup (){
    EEPROMwl.begin(EEPROM_LAYOUT_VERSION, EEPROM_INDEXES);
    readConfig(); // read profile and profileNumber  
  }

  static long lastPressedMillis = 0;
  // tactile button auto-repeat values
  static const uint8_t speed_delta[] = {1, 1, 2, 5, 10, 20, 50, 100, 0};
  static uint8_t delta_idx = 0;
  
  void loop() {
    
    readchar(); // handle serial port
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

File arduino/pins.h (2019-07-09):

#ifndef PINS_H
#define PINS_H 1
#include <Arduino.h>

/* Pin definitions. These come from the schematic.
 * Pin assignment follows the following logic:
 * - buttons are in one and the same atmega port. This allows reading all buttons in one read. (see buttons.cpp)
 * - stepper motor wires are in one and the same atmega port. This allows going to the next step in one write. (see motor_io.cpp)
 */

/*
 * On the solder paste dispenser, the led is connected to pwm-capable pin 3. 
 * On an arduino, the led is connected to not pwm-capable pin LED_BUILTIN. 
 * If you want to run this sketch on an arduino, change the following:
 * In param.h:
 * static const uint8_t kLedPin = LED_BUILTIN;
 * In breathing_led.cpp replace
 * #define LED_PWM 1
 * with
 * #define LED_PWM 0
 */

/*
 * Stepper pins are defined in tb6612.cpp
 */

/* buttons
 * All buttons are in one and the same port. (port D). 
 * This allows getting the values of the buttons reading one byte.
 * The port is hardcoded in buttons.h.
 * For port D the pin numbers are also the index of the buttons in buttons::isPressed[].
 */

// Arduino input pin for the foot pedal switch. Active low.
static const uint8_t kFootswitchPin = 2;
// Arduino input pin for the "forward" (push) button. Active low.
static const uint8_t kForwardButtonPin = 7;
// Arduino input pin for the "backward" (pull) button. Active low.
static const uint8_t kBackwardButtonPin = 4;
// Arduino input pin for the "Fast"  button. Active low.
static const uint8_t kFastButtonPin = 6;
// Arduino input pin for the "Slow" button. Active low.
static const uint8_t kSlowButtonPin = 5;

/* Led */

// Arduino pwm output pin for status led.
static const uint8_t kLedPin = 3;

#endif
// not truncated

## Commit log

2019-07-07 add bom
2019-07-07 add header
    [paste_dispenser.csv, paste_dispenser.sch]
2019-07-07 foot pedal switch
    [paste_dispenser.sch]
2019-07-08 serial console
    [paste_dispenser.csv]
2019-07-15 led blink rate
2019-07-15 led blink
2019-07-18 autodetect i2c
2019-08-13 threaded knurled brass inserts
    [coupler.stl, insert_practice.scad, insert_practice.stl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]
2019-08-14 threaded knurled tapered brass inserts
2019-09-03 add right-angle dupont
    [paste_dispenser.csv]
2019-09-14 tweak for Prusa
    [coupler.stl, insert_practice.stl, m4_threaded_insert.scad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]
2019-09-14 add pcb
    [paste_dispenser.fzz]
2019-09-21 coupler redesign
    [halfcoupler.scad, util.scad]
2019-09-21 new coupler
    [coupler.scad]
2019-09-22 rm overhangs
    [coupler.scad, coupler.stl]
2020-01-31 pic pcb
2020-02-16 fix dia
    [coupler.scad]
